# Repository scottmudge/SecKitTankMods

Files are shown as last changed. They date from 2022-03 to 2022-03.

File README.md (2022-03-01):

# SecKit Mods, Upgrades, and Repairs
 This repository contains the modifications, upgrades, and repairs to the SecKit Tank which I've created. Other modifications and repairs can be found on the primary SecKit website or wiki -- these are just those I have personally developed.
 
## Table of Contents:

### [Repairs](#repairs)
* [Constant Force Spring Replacement](#cfspring)  

<a name="repairs"/>

 ## Repairs

<a name="cfspring"/>

### Constant Force Spring Replacement (USA)

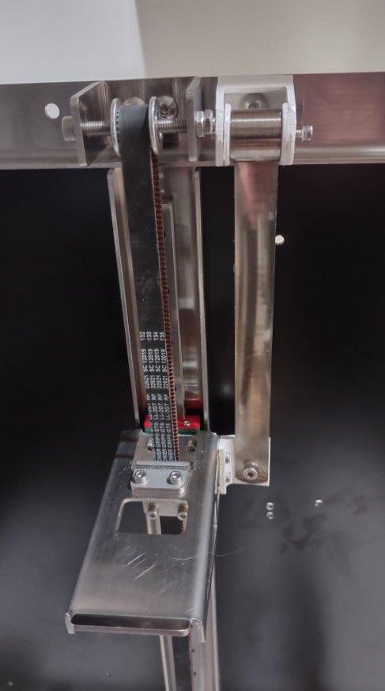
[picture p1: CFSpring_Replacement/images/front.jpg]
Replaced spring


### Incident
During assembly, I accidentally bent the constant force spring used to counter the weight of the build-plate along the z-axis. This is apparently somewhat easy to do, as all it took in my case was slightly bending the spring in a half-circular curve, roughly 10cm in diameter, opposite to the natural curl of the spring. 

I believe the issue has more to do with the natural longitudinal curve running along the length of the extended strip of the spring, sort of like a tape measure or ["snap bracelet"](https://www.thenakedscientists.com/get-naked/experiments/snap-bracelets-tape-measures-bistable-structures). This imparts a sort of bistable structure to the spring. When bent in a direction opposite to the natural "curl" of the spring, it is quite easy to create a permanent fold or "kink" in the spring.

In my case this caused a number of issues when the spring was extended and retracted. During extension, a variable amount of force was applied by the spring as the kinks were being unwound from the bobbin. It also produced an audible "click" and associated vibration as the kink/fold would unwind from the bobbin.

***Kinks in the original spring:***
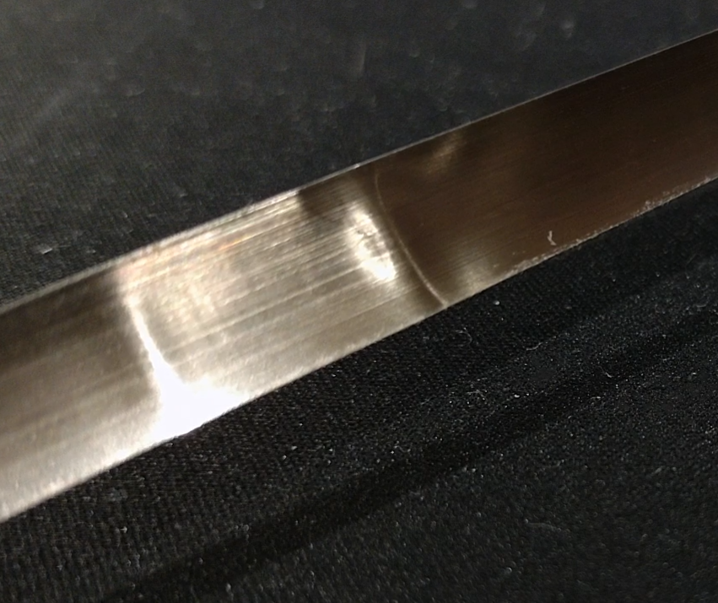
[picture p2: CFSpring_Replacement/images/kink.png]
Kinked original spring


### Issue

I've been told that the constant force spring now used in the Tank is a custom part designed specifically for the tank. It has a force of ~**1.2 kg** and a length of roughly **600mm**. 

Being in the US, shipping a tiny part like this from overseas is not worth shipping.

I could not find a part which was exactly the same dimensions or parameters, but I did find one that was sufficiently close enough which was readily available from supplier McMaster-Carr. 

This is item [9293K295](https://www.mcmaster.com/9293K295/).

At the time of writing this, it is ~$5 USD, which is pretty cheap.

Unfortunately the spring is wider and thus the attachment hole to the z-axis bed bracket does not line up with the hole used by the existing spring.

### Solution

I've created a new attachment method which re-orients the spring and provides a new attachment location, coupling the spring to the same location the original spring was connected to.

The design is such that the spring [should be perfectly vertical when extended](https://raw.githubusercontent.com/scottmudge/SecKitTankMods/master/CFSpring_Replacement/images/side.jpg), reducing the amount of unwanted lateral force.

***A diagram of the updated design:***
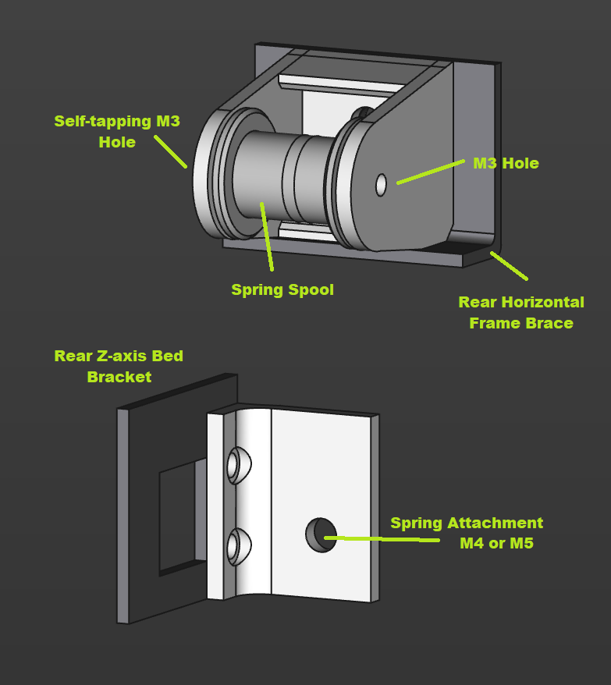
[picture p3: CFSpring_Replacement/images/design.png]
Kinked original spring


The spring is mounted to the same mount hole on the horizontal brace of the frame, but instead of extending out horizontally in the y-axis, it is parallel to the x-axis. It then attaches to a plate

### Parts

* Printed STLs (linked below)
* 10mm M3 screws (x2, and corresponding nut)
* 30mm M3 screw (no nut)
* 15-30mm M5 screw (and corresponding nut)
* 10mm M4 or M5 screw (and corresponding nut)
* New spring, item [9293K295](https://www.mcmaster.com/9293K295/) from McMaster-Carr

### Instructions

1. Print the STLs linked below. I used ASA for higher thermal resistance.
2. Assemble the bobbin so that the spring is fixed onto it. Use some CA glue or similar, but make sure the glue does not ooze out onto the spring.
3. Place the 15-30mm M5 screw through the bobbin **mount**, with the cap on the inside of the mount (the screw threads should extend to the back-side of the frame and mount). Attach and tighten bobbin bracket to the same place the old spring was attached to.
4. Place bobbin into bracket such that the **spring strip is on the back-side of the bobbin when it extends**. Fix the bobbin to the mount with the 30mm M3 screw. It should self-tap into the other side of the mount. **Do not overtighten or strip the plastic**.
5. Fix the spring attachment plate to the rear z-axis bed bracket at the same location the old spring was attached to. Use 2x 10mm M3 screws and nuts.
6. Extend the spring and attach to the attachment plate using an M4 or M5 screw (10mm or so). 

### STLs
* **[Lower Bobbin](https://raw.githubusercontent.com/scottmudge/SecKitTankMods/master/CFSpring_Replacement/stl/CFSpring-BobbinLower.stl)**
* **[Upper Bobbin](https://raw.githubusercontent.com/scottmudge/SecKitTankMods/master/CFSpring_Replacement/stl/CFSpring-BobbinUpper.stl)**
* **[Attachment Plate](https://raw.githubusercontent.com/scottmudge/SecKitTankMods/master/CFSpring_Replacement/stl/CFSpring-Joiner.stl)**
* **[Bobbin Mount](https://raw.githubusercontent.com/scottmudge/SecKitTankMods/master/CFSpring_Replacement/stl/CFSpring-Mount.stl)**

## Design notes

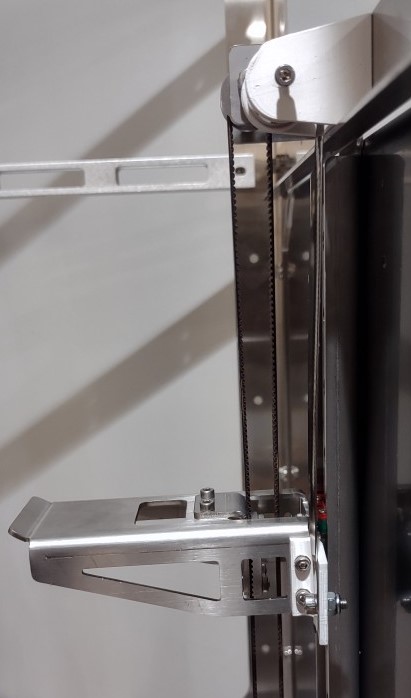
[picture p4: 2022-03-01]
CFSpring_Replacement/images/side.jpg

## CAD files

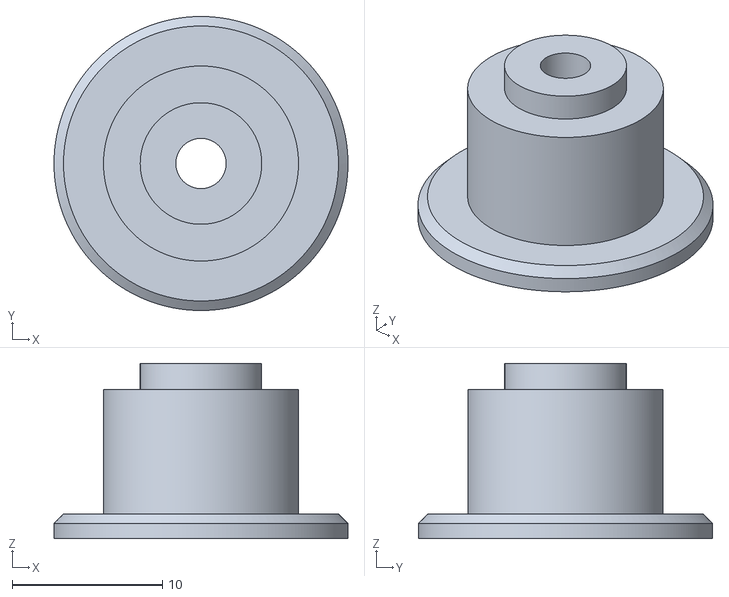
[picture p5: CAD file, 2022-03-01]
CFSpring_Replacement/stl/CFSpring-BobbinLower.stl
19.6 x 19.6 x 11.7

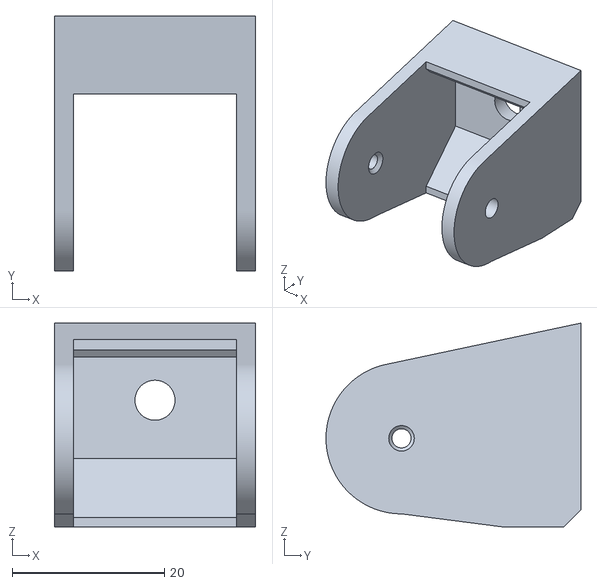
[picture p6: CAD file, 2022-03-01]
CFSpring_Replacement/stl/CFSpring-Mount.stl
26.4 x 33.5 x 26.8

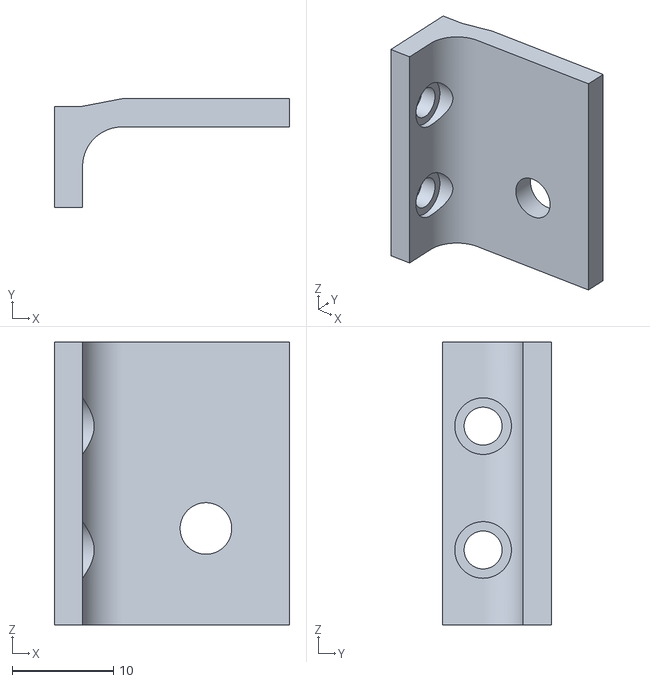
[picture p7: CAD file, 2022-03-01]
CFSpring_Replacement/stl/CFSpring-Joiner.stl
23.3 x 10.8 x 28.0

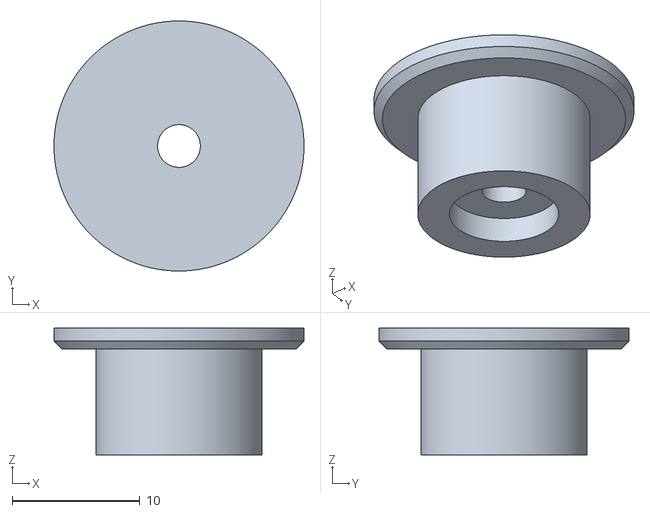
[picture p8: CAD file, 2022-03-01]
CFSpring_Replacement/stl/CFSpring-BobbinUpper.stl
19.6 x 19.6 x 9.94
